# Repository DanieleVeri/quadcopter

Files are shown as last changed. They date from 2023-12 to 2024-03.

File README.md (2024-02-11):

# Arduino quadcopter

A simple quadcopter filght controller designed to work in angle control mode ([diagram](https://docs.px4.io/v1.12/assets/img/mc_control_arch.21116ef0.jpg)).  
All parameters are grouped in `config.h`.  
Switch `OPERATING_MODE` to perform ESC calibration and IMU calibration.  
Switch `DEBUG` to visualize print messages in the serial monitor.  
The control loop frequency is about 80Hz.  

  

## Software requirements
Arduino libraries:
- MPU9250==0.4.8
- AutoPID==1.0.3

## Hardware requirements
- Board: Arduino Mega 2560
- Imu: MPU 9250
- Receiver: Flysky FS-IA6 
- Motor/ESC: A2212 1000KV Brushless Motor 30A ESC 
- Propeller: 1045
- Rangefinder: HC-SR04
- Battery: LiPo 3S 35C XT60
- DC/DC stepdown: LM7805
- 30A fuse

## Frame
- 4x motor.stl
- 4x holder.stl
- 4x hollow alluminium rod 10x10x130 mm (to link motor and holder)
- 1x plastic disk diameter ~220 mm (the base where to anchor holders with 3M bolts)
- 1x cover.stl

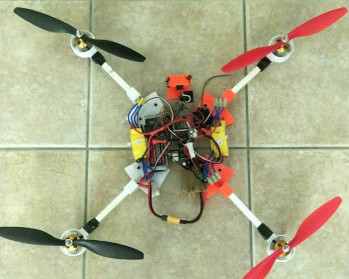
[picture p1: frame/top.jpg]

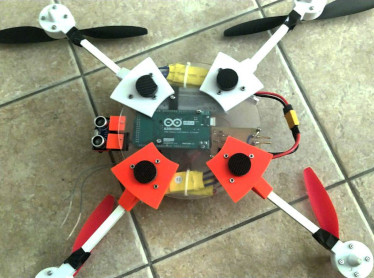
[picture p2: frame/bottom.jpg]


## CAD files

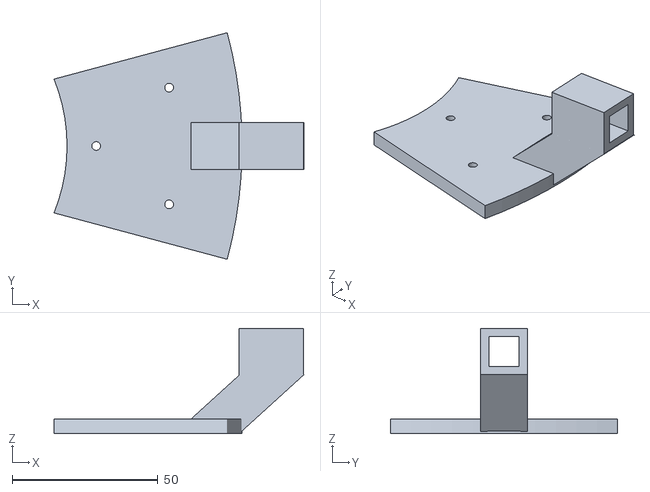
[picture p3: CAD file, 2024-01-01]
frame/holder.stl
85.7 x 77.6 x 36.0

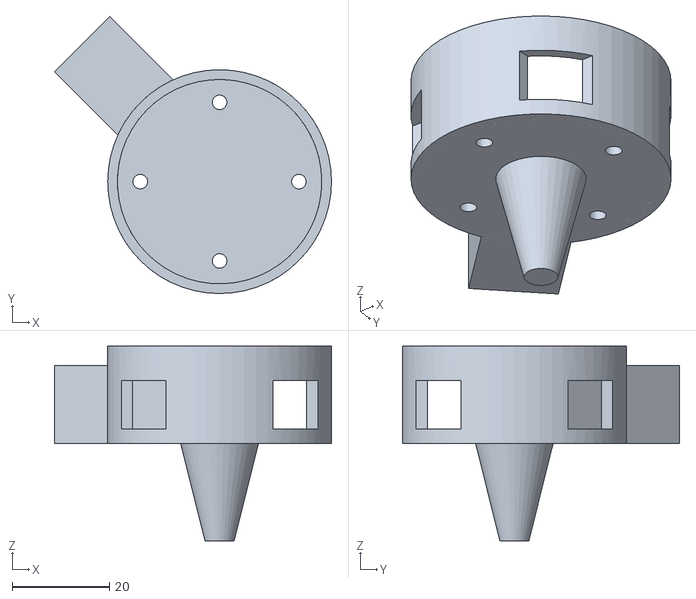
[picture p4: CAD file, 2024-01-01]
frame/motor.stl
56.9 x 56.9 x 40.0

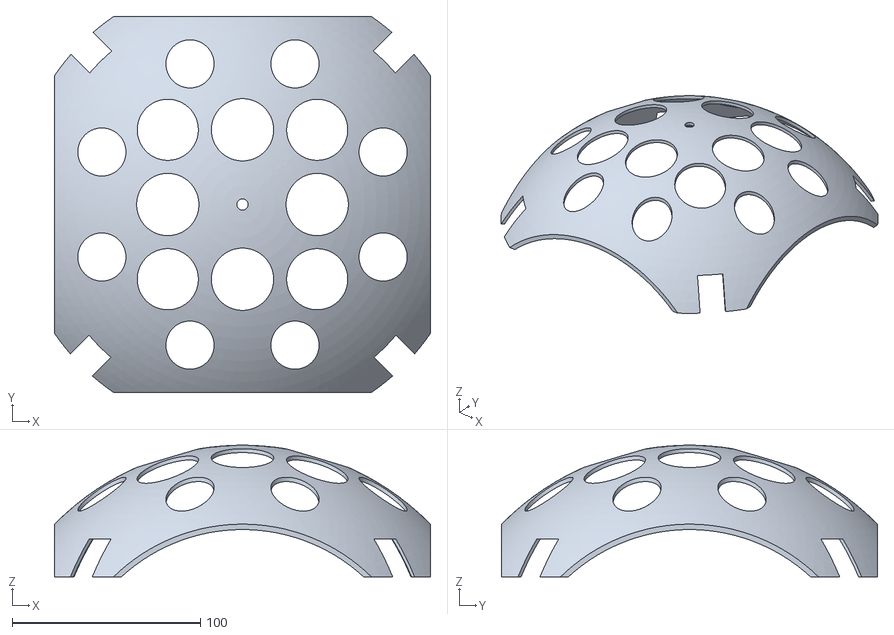
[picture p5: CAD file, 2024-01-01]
frame/cover.stl
200.0 x 200.0 x 70.0

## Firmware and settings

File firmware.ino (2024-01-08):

#include "config.h"
#include "motor.h"
#include "imu.h"
#include "flight_control.h"
#include "radio.h"
#include "rangefinder.h"


void setup() {
  Serial.begin(115200);
  Serial.println("\n Starting firmware setup...");

#if OPERATING_MODE == MODE_FLIGHT
  setup_motors();
  arm_motors();
  setup_imu();
  register_radio_interrupt();
  setup_rangefinder();
  setup_pid();
#endif

#if OPERATING_MODE == MODE_CALIB_MOTORS
  setup_motors();
  calib_motors();
#endif

#if OPERATING_MODE == MODE_CALIB_IMU
  calib_imu();
#endif

  Serial.println("\n Firmware ready");
}

void loop() {
#if OPERATING_MODE == MODE_FLIGHT
  control_loop();
#elif OPERATING_MODE == MODE_CALIB_IMU
  debug_imu();
#endif
}

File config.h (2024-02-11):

#ifndef CONFIG_H
#define CONFIG_H


// Operating modes
#define MODE_FLIGHT 0
#define MODE_CALIB_MOTORS 1
#define MODE_CALIB_IMU 2
#define OPERATING_MODE MODE_FLIGHT            // <-- set the operating mode
#define DEBUG 0                               // <-- disable motors and print debug messages

// RC bounds
#define RC_PITCH_BOUND 30                     // [-30, 30] deg
#define RC_ROLL_BOUND 30                      // [-30, 30] deg
#define RC_YAW_BOUND 90                       // [-90, 90] deg/s
#define RC_MIN_THROTTLE 1000                  // pwm
#define RC_MAX_THROTTLE 2000                  // pwm

// Altitude control
#define RANGEFINDER_MAX_DIST 400              // cm
#define GROUND_DIST_FLYING_THRESHOLD 10       // cm
#define SMOOTH_FALL_PWM 1350                  // pwm
#define START_ALTITUDE_CONTROL_THROTTLE 1400  // pwm
#define STOP_ALTITUDE_CONTROL_THROTTLE 1600   // pwm

// Sensor bias
#define IMU_TO_FRAME_ROLL 2.0                // deg
#define IMU_TO_FRAME_PITCH 2.0                // deg
#define IMU_TO_FRAME_YAW -6.0                 // deg
#define ROLL_RATE_BIAS 0.8                   // deg/s
#define PITCH_RATE_BIAS 0.9                   // deg/s
#define YAW_RATE_BIAS -1.3                    // deg/s

// PID config
#define ROLL_PID_KP 1.1
#define ROLL_PID_KI 0
#define ROLL_PID_KD 0

#define PITCH_PID_KP 1.1
#define PITCH_PID_KI 0
#define PITCH_PID_KD 0

#define ROLL_RATE_PID_KP 0.95
#define ROLL_RATE_PID_KI 0
#define ROLL_RATE_PID_KD 0.25

#define PITCH_RATE_PID_KP 0.95
#define PITCH_RATE_PID_KI 0
#define PITCH_RATE_PID_KD 0.25

#define YAW_RATE_PID_KP 5.0
#define YAW_RATE_PID_KI 0
#define YAW_RATE_PID_KD 0

#define ALTITUDE_PID_KP 200

#define OUT_MINMAX 300
#define BANGBANG 300
#define TIMESTEP 10

// Angular rate low pass filter coefficient
#define LPFD 0.2

// Motor pins
#define PIN_MOTOR_0 6       // pwm pin
#define PIN_MOTOR_1 3       // pwm pin
#define PIN_MOTOR_2 4       // pwm pin
#define PIN_MOTOR_3 5       // pwm pin

// Radio pins
#define RX_PIN_ROLL 19      // interrupt pin
#define RX_PIN_PITCH 18     // interrupt pin
#define RX_PIN_YAW 2        // interrupt pin
#define RX_PIN_THROTTLE 9   // pwm pin
#define RX_PIN_AUX1 10      // pwm pin (unused)
#define RX_PIN_AUX2 11      // pwm pin (unused)

// Rangefinder pins
#define TRIGGER_PIN 45      // pwm pin
#define ECHO_PIN 37

#endif

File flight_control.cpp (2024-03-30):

#include "Arduino.h"
#include "AutoPID.h"
#include "flight_control.h"
#include "imu.h"
#include "radio.h"
#include "motor.h"
#include "rangefinder.h"


// State variables
static Linear acc;
static Attitude angles;
static Attitude rates;
static Attitude filtered_rates;
static double ground_dist = 0;

// RC input
static Attitude angles_setpoint;
static int rc_throttle = 0;

// Control values
static Attitude rates_setpoint;  // --> angles_output
static Attitude rates_output;
static const double acc_setpoint = 1;
static double acc_correction = 0;

// Outputs
static int output_throttle = 0;
static int mixer_output[4] = { 0, 0, 0, 0 };

// PID controllers
static AutoPID PID_altitude_control(&acc.z, &acc_setpoint, &acc_correction,
                                    -OUT_MINMAX, OUT_MINMAX,
                                    ALTITUDE_PID_KP, 0, 0);

static AutoPID PID_roll_angle(&angles.roll, &angles_setpoint.roll, &rates_setpoint.roll,
                              -OUT_MINMAX, OUT_MINMAX,
                              ROLL_PID_KP, ROLL_PID_KI, ROLL_PID_KD);

static AutoPID PID_pitch_angle(&angles.pitch, &angles_setpoint.pitch, &rates_setpoint.pitch,
                               -OUT_MINMAX, OUT_MINMAX,
                               PITCH_PID_KP, PITCH_PID_KI, PITCH_PID_KD);

static AutoPID PID_roll_rate(&filtered_rates.roll, &rates_setpoint.roll, &rates_output.roll,
                             -OUT_MINMAX, OUT_MINMAX,
                             ROLL_RATE_PID_KP, ROLL_RATE_PID_KI, ROLL_RATE_PID_KD);

static AutoPID PID_pitch_rate(&filtered_rates.pitch, &rates_setpoint.pitch, &rates_output.pitch,
                              -OUT_MINMAX, OUT_MINMAX,
                              PITCH_RATE_PID_KP, PITCH_RATE_PID_KI, PITCH_RATE_PID_KD);

static AutoPID PID_yaw_rate(&filtered_rates.yaw, &rates_setpoint.yaw, &rates_output.yaw,
                            -OUT_MINMAX, OUT_MINMAX,
                            YAW_RATE_PID_KP, YAW_RATE_PID_KI, YAW_RATE_PID_KD);

void get_radio_input() {
  sample_throttle();
  rc_throttle = map(get_rx_throttle(), MIN_PULSE_LENGTH, MAX_PULSE_LENGTH, RC_MIN_THROTTLE, RC_MAX_THROTTLE);
  angles_setpoint.roll = map(get_rx_roll(), MIN_PULSE_LENGTH, MAX_PULSE_LENGTH, -RC_ROLL_BOUND, RC_ROLL_BOUND);
  angles_setpoint.pitch = map(get_rx_pitch(), MIN_PULSE_LENGTH, MAX_PULSE_LENGTH, RC_PITCH_BOUND, -RC_PITCH_BOUND);
  rates_setpoint.yaw = map(get_rx_yaw(), MIN_PULSE_LENGTH, MAX_PULSE_LENGTH, -RC_YAW_BOUND, RC_YAW_BOUND);
}

static uint32_t last_connected_ts = 0;

void control_loop() {
  sample_throttle();
#if DEBUG
  const bool radio_connected = true;
#else
  const bool radio_connected = (get_rx_throttle() > 0);
#endif

  // Radio input
  bool lost_signal = false;
  if (radio_connected) {
    last_connected_ts = millis();
    get_radio_input();
  } else {
    // Allow lost of signal < 1s
    if (millis() - last_connected_ts > 1000) {
      lost_signal = true;
    }
  }

  if (!lost_signal) {
    // Update state
    get_angles(angles);
    get_linear_acc(acc, angles);
    get_rates(rates);
    low_pass_filter(rates, filtered_rates);
    get_range(ground_dist, angles);

    // Compute PID
    PID_altitude_control.run();
    PID_roll_angle.run();
    PID_pitch_angle.run();
    PID_roll_rate.run();
    PID_pitch_rate.run();
    PID_yaw_rate.run();

    // Altitude control
    const bool is_flying = (ground_dist > GROUND_DIST_FLYING_THRESHOLD && ground_dist < RANGEFINDER_MAX_DIST);
    const bool maintain_altitude = (rc_throttle > START_ALTITUDE_CONTROL_THROTTLE && rc_throttle < STOP_ALTITUDE_CONTROL_THROTTLE);
    if (maintain_altitude && is_flying) {
      output_throttle = rc_throttle - acc_correction;
    } else {
      output_throttle = rc_throttle;
    }

    // Prevent free fall from more than 10cm
    if (is_flying)
      output_throttle = max(rc_throttle, SMOOTH_FALL_PWM);

    // Thrust correction depending on attitude
    output_throttle = MIN_PULSE_LENGTH + ((float)(output_throttle - MIN_PULSE_LENGTH)) / (cos(angles.roll * DEG_TO_RAD) * cos(angles.pitch * DEG_TO_RAD));

    // Mixer
    mixer_output[0] = output_throttle + (rates_output.roll) + (rates_output.pitch) + rates_output.yaw;
    mixer_output[1] = output_throttle - (rates_output.roll) + (rates_output.pitch) - rates_output.yaw;
    mixer_output[2] = output_throttle + (rates_output.roll) - (rates_output.pitch) - rates_output.yaw;
    mixer_output[3] = output_throttle - (rates_output.roll) - (rates_output.pitch) + rates_output.yaw;

  } else {
    // Reset state
    acc.reset();
    angles.reset();
    rates.reset();
    filtered_rates.reset();
    angles_setpoint.reset();
    rates_setpoint.reset();
    angles_setpoint.reset();

    // Reset PID
    PID_altitude_control.stop();
    PID_roll_angle.stop();
    PID_pitch_angle.stop();
    PID_roll_rate.stop();
    PID_pitch_rate.stop();
    PID_yaw_rate.stop();

    // Zero the mixer output
    memset(mixer_output, 0, sizeof(int) * 4);
  }

  // Power the motors
#if !DEBUG
  set_motor_values(mixer_output);
#endif

#if DEBUG
  debug_state();
#endif
}

void setup_pid() {
  PID_altitude_control.setTimeStep(TIMESTEP);
  PID_altitude_control.setBangBang(BANGBANG);

  PID_roll_angle.setTimeStep(TIMESTEP);
  PID_roll_angle.setBangBang(BANGBANG);
  PID_pitch_angle.setTimeStep(TIMESTEP);
  PID_pitch_angle.setBangBang(BANGBANG);

  PID_roll_rate.setTimeStep(TIMESTEP);
  PID_roll_rate.setBangBang(BANGBANG);
  PID_pitch_rate.setTimeStep(TIMESTEP);
  PID_pitch_rate.setBangBang(BANGBANG);
  PID_yaw_rate.setTimeStep(TIMESTEP);
  PID_yaw_rate.setBangBang(BANGBANG);
}

void debug_state() {
  static uint32_t prev_ms = 0;
  static uint32_t ticks = 0;
  ticks++;
  if (millis() - prev_ms < 500)
    return;
  prev_ms = millis();
    Serial.println("======== DEBUG STATE ========");
  Serial.print("Ticks: ");
  Serial.println(ticks);
  ticks = 0;
  Serial.println("Linear acceleration (g)");
  acc.print();
  Serial.print("Ground distance (cm): ");
  Serial.println(ground_dist);
  Serial.print("Acc z correction (cm): ");
  Serial.println(acc_correction);
  Serial.println("Angles (deg)");
  angles.print();
  Serial.println("Rates (deg/s)");
  rates.print();
  Serial.println("Filtered rates (deg/s)");
  filtered_rates.print();
  Serial.print("Throttle RC (pwm): ");
  Serial.println(rc_throttle);
  Serial.print("Throttle output (pwm): ");
  Serial.println(output_throttle);
  Serial.println("Angles setpoints (deg)");
  angles_setpoint.print();
  Serial.println("Rates setpoints (deg/s)");
  rates_setpoint.print();
  Serial.println("Rates outputs (deg/s)");
  rates_output.print();
  Serial.println("Motor outputs (pwm)");
  for (int i = 0; i < 4; i++) {
    Serial.print(mixer_output[i]);
    Serial.print("  ");
  }
  Serial.print("\n");
}
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

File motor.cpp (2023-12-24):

#include "motor.h"


static Servo mot0, mot1, mot2, mot3;


void displayInstructions() {
  Serial.println("READY - PLEASE SEND INSTRUCTIONS AS FOLLOWING :");
  Serial.println("\t0 : Send min throttle");
  Serial.println("\t1 : Send max throttle");
  Serial.println("\t2 : Run test function\n");
}

void setup_motors() {
  mot0.attach(PIN_MOTOR_0, MIN_PULSE_LENGTH, MAX_PULSE_LENGTH);
  mot1.attach(PIN_MOTOR_1, MIN_PULSE_LENGTH, MAX_PULSE_LENGTH);
  mot2.attach(PIN_MOTOR_2, MIN_PULSE_LENGTH, MAX_PULSE_LENGTH);
  mot3.attach(PIN_MOTOR_3, MIN_PULSE_LENGTH, MAX_PULSE_LENGTH);
}

void calib_motors() {
  displayInstructions();
  if (Serial.available()) {
    char data;
    data = Serial.read();

    switch (data) {
      // 0
      case 48:
        Serial.println("Sending minimum throttle");
        mot0.writeMicroseconds(MIN_PULSE_LENGTH);
        mot1.writeMicroseconds(MIN_PULSE_LENGTH);
        mot2.writeMicroseconds(MIN_PULSE_LENGTH);
        mot3.writeMicroseconds(MIN_PULSE_LENGTH);
        break;

      // 1
      case 49:
        Serial.println("Sending maximum throttle");
        mot0.writeMicroseconds(MAX_PULSE_LENGTH);
        mot1.writeMicroseconds(MAX_PULSE_LENGTH);
        mot2.writeMicroseconds(MAX_PULSE_LENGTH);
        mot3.writeMicroseconds(MAX_PULSE_LENGTH);
        break;

      // 2
      case 50:
        Serial.print("Running test in 3");
        delay(1000);
        Serial.print(" 2");
        delay(1000);
        Serial.println(" 1...");
        delay(1000);

        for (int i = MIN_PULSE_LENGTH; i <= MAX_PULSE_LENGTH; i += 5) {
          Serial.print("Pulse length = ");
          Serial.println(i);
          mot0.writeMicroseconds(i);
          mot1.writeMicroseconds(i);
          mot2.writeMicroseconds(i);
          mot3.writeMicroseconds(i);
          delay(200);
        }

        Serial.println("STOP");
        mot0.writeMicroseconds(MIN_PULSE_LENGTH);
        mot1.writeMicroseconds(MIN_PULSE_LENGTH);
        mot2.writeMicroseconds(MIN_PULSE_LENGTH);
        mot3.writeMicroseconds(MIN_PULSE_LENGTH);
        break;
    }
  }
}

void arm_motors() {
  mot0.writeMicroseconds(MIN_PULSE_LENGTH);
  mot1.writeMicroseconds(MIN_PULSE_LENGTH);
  mot2.writeMicroseconds(MIN_PULSE_LENGTH);
  mot3.writeMicroseconds(MIN_PULSE_LENGTH);
}

void set_motor_values(int *mixer_output) {
  mot0.writeMicroseconds(mixer_output[0]);
  mot1.writeMicroseconds(mixer_output[1]);
  mot2.writeMicroseconds(mixer_output[2]);
  mot3.writeMicroseconds(mixer_output[3]);
}

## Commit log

2023-09-14 using radio interrupts
2023-09-17 start tuning pid
2023-09-19 switch pid library
2023-10-06 change pins; minor fixes
    [config.h, flight_control.cpp, imu.cpp]
2023-10-09 decent pid
2023-12-24 add imu frame correction
    [config.h, flight_control.cpp, imu.cpp]
2023-12-25 fix imu calib
2023-12-26 add debug switch
2023-12-27 pid tuning okish
2024-01-01 add attitude thrust compensation
2024-01-01 add frame
    [cover.stl, holder.stl, motor.stl]
2024-02-11 fix acceleration and angle correction
    [config.h, imu.cpp]
